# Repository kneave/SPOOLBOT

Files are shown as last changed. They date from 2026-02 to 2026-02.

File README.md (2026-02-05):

# SPOOLBOT
Prusa 2KG Spool Robot

Source Code, Wiring Diagram & BOM for SpoolBot.
Arduino Code is Running on a DF-Robot Romeo Mini ESP32.

Check out the origonal build video here:
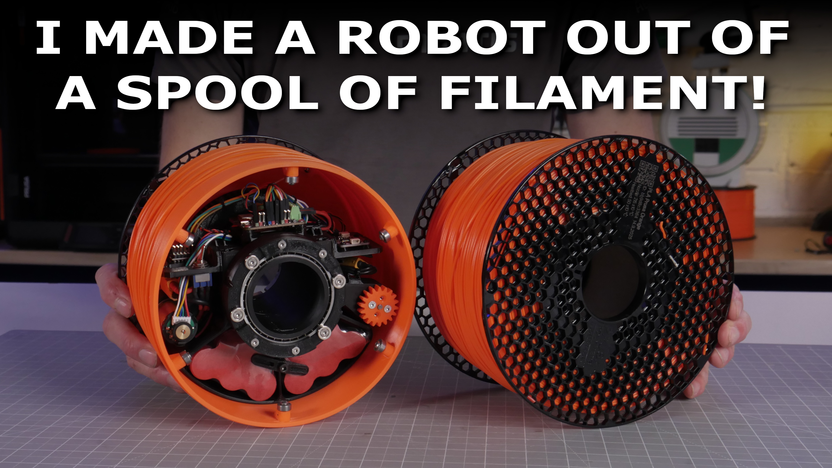
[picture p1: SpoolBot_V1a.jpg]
Watch the video (https://youtu.be/6ZLJA1YpoMs)


STL & CAD Files available at Printables.com
https://www.printables.com/@mantisrobot_2496648
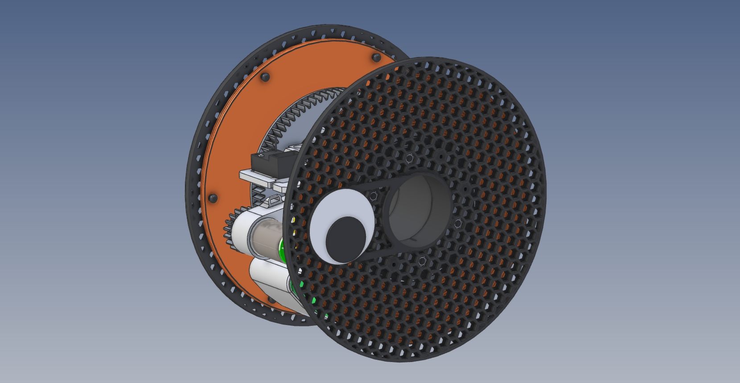
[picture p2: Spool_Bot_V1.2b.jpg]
SpoolBot


SpoolBot Scematic
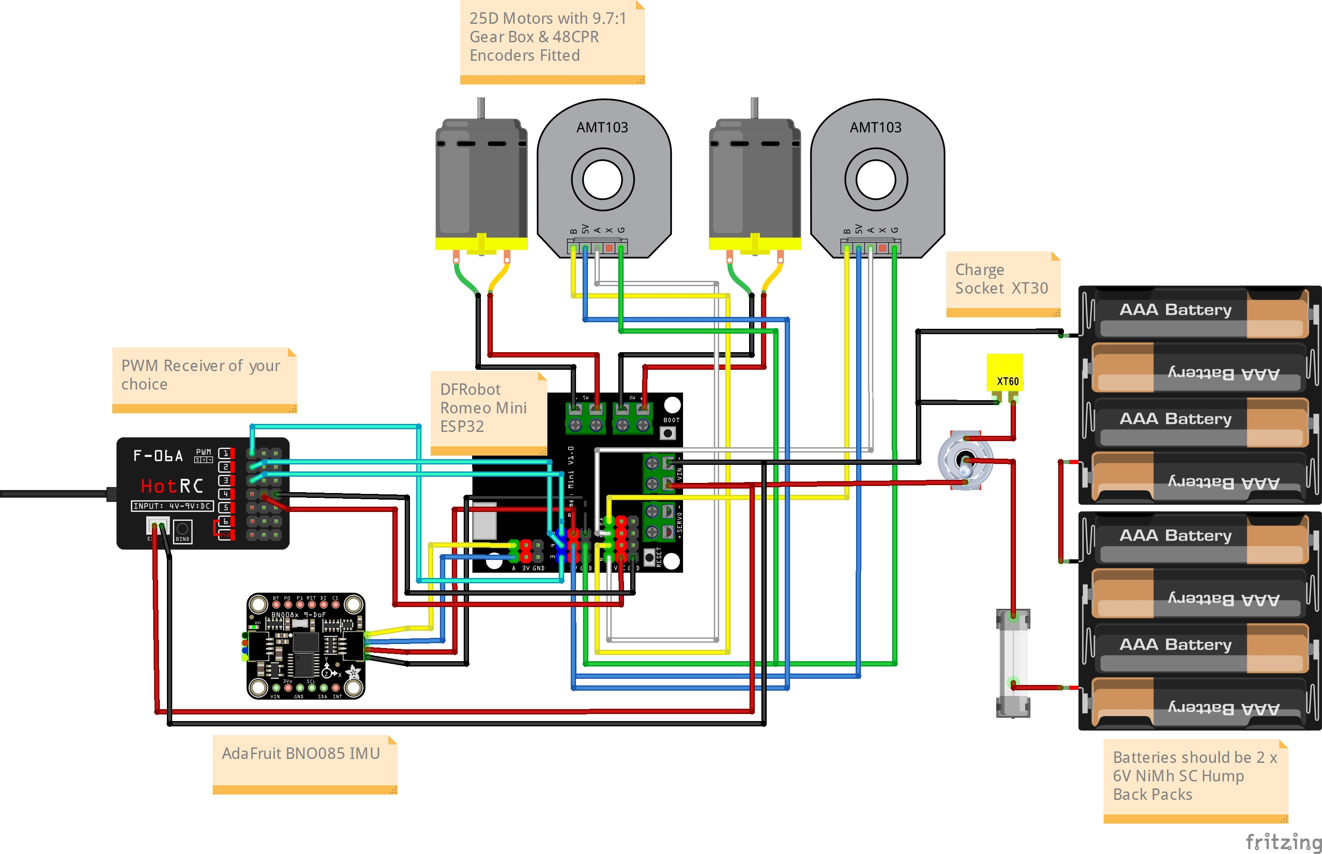
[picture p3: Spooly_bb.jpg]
schematic Schematic


## Parts List
Reference links provided in the [Parts List](./Prusa%20Spool%20Bot%20BOM.xlsx)

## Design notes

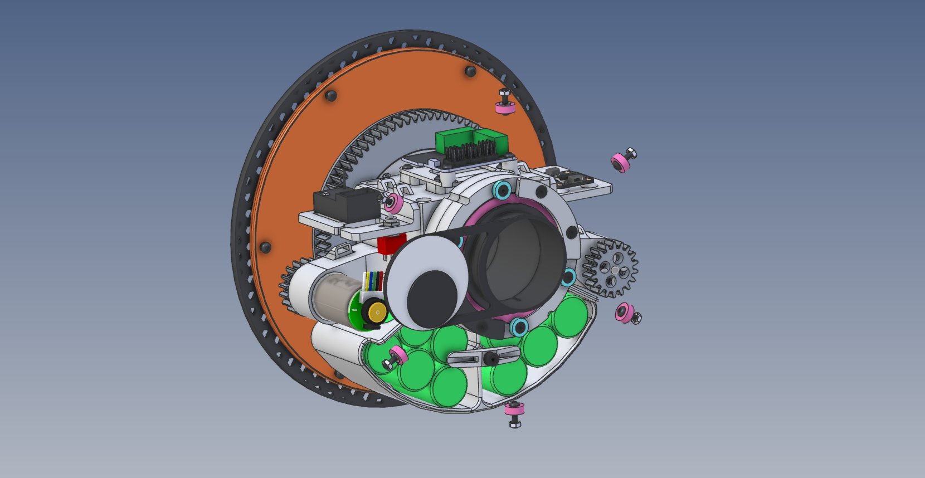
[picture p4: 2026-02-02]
Spool_Bot_V1.2.jpg

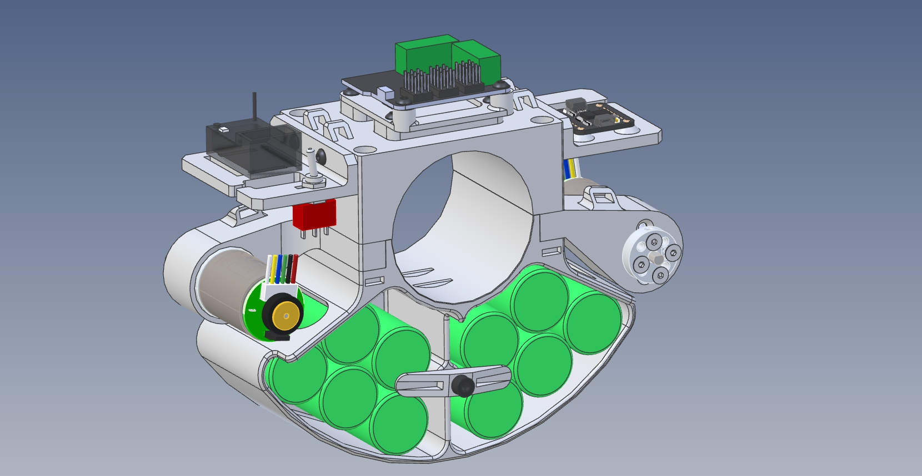
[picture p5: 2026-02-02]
Central_Hub.jpg

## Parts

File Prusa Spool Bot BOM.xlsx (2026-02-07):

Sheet: BOM
Prusa Spool Bot BOM
Part | Description | Qty | Cost | Sub | UK Links | U.S. Links | Notes
1 | 55x68x7mm Bearing 61711 | 4 | £6.73 | £26.92 | 61711 Bearing (https://simplybearings.co.uk/shop/p188629/61711-Budget-Open-Type-Thin-Section-Deep-Groove-Ball-Bearing-55x68x7mm/product_info.html) | https://amzn.to/4qeRzQE | (Shop around local for cheaper)
2 | 10x3x4 Bearing | 6 | £2.23 | £13.38 | 10x3x4 Bearing (https://simplybearings.co.uk/shop/p170604/623ZZ-Budget-Metal-Shielded-Deep-Groove-Ball-Bearing-3x10x4mm/product_info.html) | https://amzn.to/4ajuCWC | (Unknown quality!)
3 | Motor/Encoder | 2 | £61.95 | £123.90 | https://www.pololu.com/product/4862 | https://www.pololu.com/product/4862
4 | Hub Adapter | 1 | £10.95 | £10.95 | https://www.pololu.com/product/1997 | https://www.pololu.com/product/1997
 | M3 Button Head Set | 1 | £5.99 | £5.99 | https://amzn.to/4q6ULh3 | https://amzn.to/4a8HcYu
5 | M3x6 Button Head Socket | 13
6 | M3x12 Button Head | 10
7 | M3x7x0.5 washer | 6
 | M3 Counter Sunk Set | 1 | £5.58 | £5.58 | https://amzn.to/4ragjKA | https://amzn.to/4qXbHI8
8 | M3x6 CS Screw | 12
9 | M3x20 CS Socket | 12
10 | M3 Hex Nut | 6
 | M4 Cap Head Set | 1 | £5.00 | £5.00 | https://amzn.to/4qMgcFp | https://amzn.to/3O3PfhM
11 | M4x25 Cap Head | 9
12 | M4x5 Black cap head | 8 | £3.79 | £3.79 | https://amzn.to/45wr8ye | https://amzn.to/4roa8Tb
13 | M4x8 CS + Nut Black | 4 | £6.58 | £6.58 | https://amzn.to/45ueRdQ | https://amzn.to/4qVIehy
14 | M4 Square Nut | 4
15 | M4 Hex Nut | 8
16 | No.2 x 6.4mm Screw | 4 | £1.39 | £1.39 | https://amzn.to/4bmNia4 | https://amzn.to/4taD7Md
17 | 12x3x4 Magnets | 4 | £9.98 | £9.98 | https://amzn.to/4sokrs0 | https://amzn.to/4c5deai
18 | 10x3x3 Magnets | 4 | £9.99 | £9.99 | https://amzn.to/4qDw7Wc | https://amzn.to/4qhv7q1
19 | 50mm Goolgy Eyes | 1 | £4.19 | £4.19 | https://amzn.to/3YJqABu | https://amzn.to/4aso4G6
20 | M3 Heat Insert | 29
21 | M4 Heat Insert | 5
22 | DF Robot Romeo ESP32 | 1 | £17.00 | £17.00 | DF Robot Romeo ESP32 (https://uk.farnell.com/dfrobot/dfr1063/romeo-mini-control-board-esp32/dp/445737)
23 | 6A Toggle Switch (ON-ON) | 1 | £6.99 | £6.99 | https://amzn.to/3YJVCch | https://amzn.to/4r3gBDC
24 | 18 AWG silicone wire | 1 | £5.99 | £5.99 | https://amzn.to/4qwDm1Z | https://amzn.to/4acHDRK
25 | XT60 Male Connector | 2 | £5.49 | £5.49 | https://amzn.to/4bJrepZ | https://amzn.to/4kcfxKM
26 | Jumper F-F 100mm | 10 | £6.99 | £6.99 | https://amzn.to/49Qc7sr | https://amzn.to/3OiPnKm
27 | Qwiic Connector Jumper | 1 | £1.00 | £1.00 | Qwiic Jumper (https://thepihut.com/products/stemma-qt-qwiic-jst-sh-4-pin-cable-with-premium-female-sockets-150mm-long) | https://www.adafruit.com/product/4397
28 | 6V NiMh Battery Hump Back | 2 | £14.35 | £28.70 | 6V NiMh Battery (https://www.componentshop.co.uk/6v-3300mah-sc-nimh-hump-rc-battery-pack-vapex.html) |  | (Local R/C Shop? 3000 TO 5000MaH)
29 | Adafruit BNO085 | 1 |  | £27.00 | https://amzn.to/4rjBVnJ | https://www.adafruit.com/product/4754
30 | Dupont 0.1” Connector Kit | 1 |  | £7.89 | https://amzn.to/4rjBVnJ | https://amzn.to/49XTeVK
31 | Top RC Transmitter | 1 | £29.89 | £29.89 | https://www.amazon.co.uk/Transmitter-Receiver-Remote-Controller-Channel/dp/B0CH17GR5Y?th=1 | https://www.amazon.com/DS-600-Transmitter-Receiver-Controller-Channel/dp/B09Y8XT53X
32 | Prusament PLA/PETG | 1 | 23.99 | 23.99 |  | https://amzn.to/4a9z8Xh
33 | Prusament PETG | 1 | 23.99 | 23.99 |  | https://amzn.to/3NTPufy
 |  |  |  | £412.56

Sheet: 3D Printed Parts
Item | Name | Qty | Material | Notes
1 | DHG M1.5 18T | 2 | PLA
2 | Fake Side Filament Removable End | 1 | PLA
3 | Fake Side Filament V1.1 | 1 | PLA
4 | Filament Hub V1.1 | 1 | PLA
5 | Removable Side Shim | 1 | PLA
6 | Axle Body Spacer | 2 | PETG
7 | Spool Bearing Holder MAG P2 | 1 | PETG | Magnetic Side (Left)
8 | Spool Bearing Holder MAG P3 | 1 | PETG | Magnetic Side (Left)
9 | Spool Bearing Holder P1 | 2 | PETG | Magnetic Side (Left)
10 | Spool Bearing Holder P1 Fixed | 1 | PETG | Fixed Side (Right)
11 | Spool Bearing Holder P2 | 1 | PETG | Fixed Side (Right)
12 | Spool Bearing Holder P3 | 1 | PETG | Fixed Side (Right)
13 | Axle Lock V1 | 2 | PETG
14 | Battery Mount | 1 | PETG
15 | Battery Stay | 1 | PETG
16 | Central Hub Clamp V1.1 | 1 | PETG
17 | Central Hub | 2 | PETG
18 | IMU Shelf | 1 | PETG
19 | Motor Mount | 2 | PETG
20 | Romeo Mini Mount V1.1 | 1 | PETG
21 | RX Shelf | 1 | PETG
22 | Spool Gear Hub Fixed Side UNITE | 1 | PETG | (Right side)
23 | Spool Gear Hub UNITE 80T | 1 | PETG | (Left Side)
24 | Googly Eye Adapter | 2 | PETG
 | Total Parts | 31

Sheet: Loom
LOOM
Main black and red wire between connectors 300mm long
Short red wire from XT60 to switch middle pin 110mm
Red power wire to terminal block 250mm cut to length
Black charge wire from negative 200mm cut to length
Black power wire from negative 200mm cut to length
Red charge wire from switch 150mm cut to length

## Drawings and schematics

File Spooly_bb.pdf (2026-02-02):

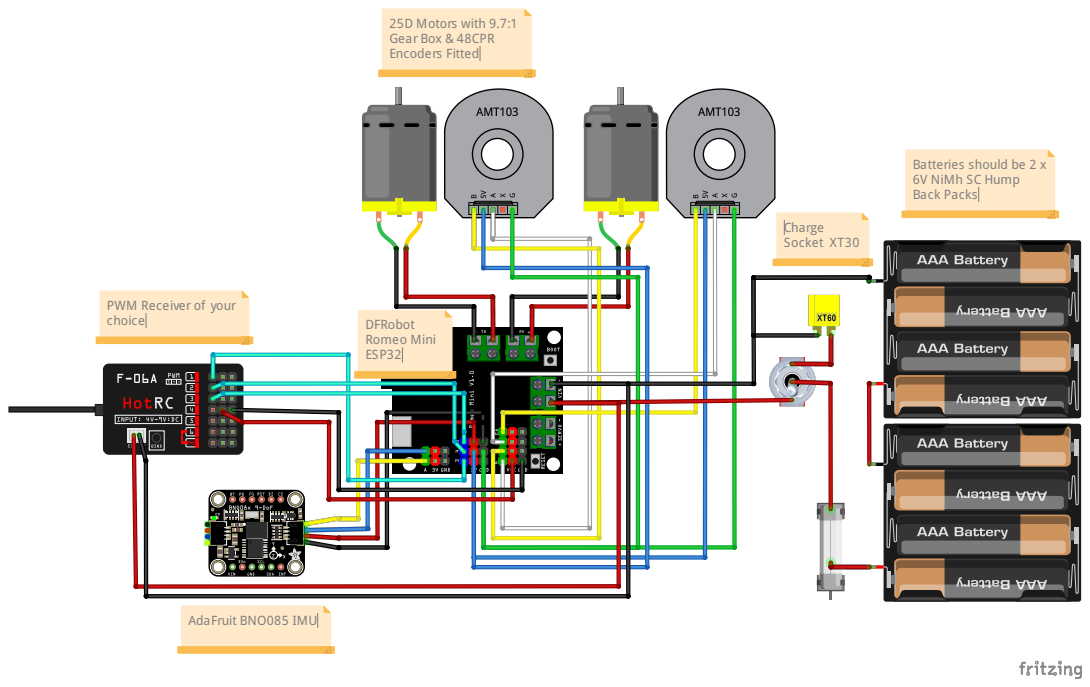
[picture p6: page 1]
Charge Socket XT30; 25D Motors with 9.7:1 Gear Box & 48CPR Encoders Fitted; AdaFruit BNO085 IMU; DFRobot Romeo Mini ESP32

Batteries should be 2 x
6V NiMh SC Hump
Back Packs

PWM Receiver of your
choice

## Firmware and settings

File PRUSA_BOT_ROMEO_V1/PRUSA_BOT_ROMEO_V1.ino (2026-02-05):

// *****************************************************
//  Prusa Spool Bot (Spooly) by Matt Denton 05/02/2026
//  Written for DFRobot Romeo Mini ESP32.
//  Used "ESP32C3 Dev Module" as the device selection.
//  Enable "USB CDC On Boot" for USB debug messages.
//  Requires Adafruit BNO085 IMU.
//
//  Removeable / Magenetc side is the left, Fixed side is right
//  
//  PWM Inputs will require calibration, use the USBC connector to access the serial terminal
//  type 'C' and press enter in the console and follow instructions.
//
//  Some know issues with BNO085 and ESP32 i2c. if you are having problems try adding a 2K2 to 4k7 
//  resistor on the BNO085 from VCC to SDA line
//
// *****************************************************

#include <Arduino.h>
#include <Adafruit_BNO08x.h>
#include <PID.h>
#include <WiFi.h>
#include <WiFiUdp.h>
#include <ArduinoOTA.h>  // For enabling over the air updates
#include "DFRobot_GDL.h"
#include <EEPROM.h>

//  Loop Frequency
#define LOOP_TIME 10 //ms

// *****************************************************
// FEATURE DEFINITIONS

//#define ENABLE_OTA        // Over The Air Updates, switch off once tuning/development is done
//#define ENABLE_UDP_DEBUG  // send / receive UDP debug data for tuning, switch off once tuning is done.
IPAddress pcIP(10,1,0,123);   // your PC IP address for SerialPlot

#define USE_LEDC          // ledcWrite routines rather than analogWrite for Motor PWM
#define PWM_FREQUENCY_SWITCHING // without this only MOTOR_PWM_LO_FREQUENCY is used
#define PWM_HI_FREQ_DUTY         (0.1f) // NORMALISED SO 0.1 = 10%
#define PWM_LO_FREQ_DUTY         (0.05f) // NORMALISED SO 0.05 = 5%
#define MOTOR_PWM_HI_FREQUENCY   8000 // Above PWM_HI_FREQ_DUTY dutr this frequency is used
#define MOTOR_PWM_LO_FREQUENCY   2000 // Belwo PWM_LO_FREQ_DUTY duty this frequency is used

// *****************************************************
// MOTOR SPEED / CONTROL VARIABLES

#define ENC_CPR (48.0f)
#define MOTOR_GEAR_RATIO  (9.7f) // motor attached gearbox
#define PRINTED_GEAR_RATIO  (80.0f/18.0f)

#define MOTOR_MAX_RPM       (8000) // before gearbox, this determines max forward speed
#define RPM_DEADBAND        (100) // RPM
#define MIN_RPM             (0) // provides kick if needed
#define MAX_TURN_SPEED      (540.0f) // degreees /sec

#define TURN_FORWARD_SPEED_REDUCTION 0.35f // reduction in forward speed when turning, this is a sliding scale from 100% to this value.
#define PITCH_CURVE 0.35f                 // IMU Pitch sigmoid curve, lower values = higher brakeing, 1 = linear 
#define HALF_SPEED_REDUCTION      (0.6f)  // user control speed reduction for forward / reverse
#define HALF_SPEED_TURN_REDUCTION (0.6f)  // user control speed reduction for turn

// *****************************************************
// IMU / CONTROL VARIABLES USED FOR NORMALISING IMU DATA

#define IMU_PITCH_MAX (75.0f) // at this angle the motor is in full reverse to prevent looping
#define IMU_ROLL_MAX (50.0f)  // fall/tilt angle motors off 
#define IMU_YAW_MAX (50.0f)
#define IMU_PITCH_RATE_MAX (360.0f)
#define IMU_ROLL_RATE_MAX (360.0f)
#define IMU_YAW_RATE_MAX (MAX_TURN_SPEED) // determins max turn speed

// *****************************************************
//  PINS

#define MOTA_ENCA  6
#define MOTA_ENCB  7
#define MOTB_ENCA  20
#define MOTB_ENCB  21

#define PWM_PITCH  4
#define PWM_YAW    3
#define PWM_AUX    5

#define MOTA_DIR   1
#define MOTA_PWM   0
#define MOTB_DIR   10
#define MOTB_PWM   2

// *****************************************************
//  PID VARIABLES & INSTANCES

// left motor / magnetic removable side
float  lDesiredRpm=0, lMeasuredRpm=0, lDriveOutput=0;
std::PID lPid(&lMeasuredRpm, &lDriveOutput, &lDesiredRpm,3.2f,6.8f,0.12f, DIRECT); // 0.00012, 0.0005
// right motor / fixed side
float  rDesiredRpm=0, rMeasuredRpm=0, rDriveOutput=0;
std::PID rPid(&rMeasuredRpm, &rDriveOutput, &rDesiredRpm,3.2f,6.8f,0.12f, DIRECT); // 0.2, 3.5, 0.001
// turn PID
float  measuredYaw=0, setYaw=0, yawOutput=0;
std::PID yawPid(&measuredYaw, &yawOutput, &setYaw,0.35f,2.0f,0.005f, DIRECT); // 0.2, 3.5, 0.001

// variables sued in control caluculations and in experimental speed PID
float pitchOutput=0,measuredSpeed=0;


// *****************************************************
// trim variables used during remote tuning of PID loops
float trimTemp = PITCH_CURVE;
float pTrim = 0.001;
float iTrim = 0.012f;
float dTrim = 0.0f;

#define PTRIM_INC 0.0001f  // 0.05
#define ITRIM_INC 0.001f  // 0.05
#define DTRIM_INC 0.00001f // 0.001

// *****************************************************
//  IMU

Adafruit_BNO08x  bno08x(-1);
sh2_SensorValue_t sensorValue;


// *****************************************************
// global variables

unsigned long previousMillis = 0;
bool  initialBoot = true; // must be cleared by user input before motors can be enabled on initial boot.
bool  motorsEnabled = false;  // user motor kill switch
bool  headingHoldAlways = false;  // hold heading even when no user input
bool  positionHoldAlways = true;  // hold position rather than drift if nudged
bool  userControl = false; // is there a desired move from user controls
bool  halfSpeed = false;  // finer speed control
bool  halfSpeedTurn = true;  // finer speed control

float  normPitch=0,normRoll=0,normPitchRate=0,normYawRate=0,pitchCurve=0;
float  measuredSpeedFiltered=0;

// encoder outputs
float EncA_SpeedFiltered = 0; // filtered encoder speeds
float EncB_SpeedFiltered = 0;
float WheelA_OutputSpeed = 0; // calculated wheel speeds
float WheelB_OutputSpeed = 0;

// loop delta variables
uint32_t  loopLastUs = 0;
uint32_t  loopDeltaUs = 0;
float loopDelta = 0;

// user controls
uint16_t  pitch_PWM = 1500;
uint16_t  yaw_PWM = 1500;
uint16_t  aux_PWM = 1500;
float pitch_controlFiltered = 0;  // filtered user controls
float yaw_controlFiltered = 0;
float aux_controlFiltered = 0;
float pitch_controlFinal = 0;     // final user controls after all filters applied
float yaw_controlFinal = 0;

// Gyro Structure
typedef struct {
  float x;
  float y;
  float z;
} gyro_s;

// gyro filtered data
gyro_s gyroF;

// *****************************************************
// Calibration data

struct __attribute__((packed)) PWMCal {
  uint16_t min_raw;   // 
  uint16_t max_raw;   // 
  uint16_t mid_raw;   // 
};

struct __attribute__((packed)) CalStore {
  uint32_t magic;     // 0x50454431 
  PWMCal pitch;
  PWMCal yaw;
  uint16_t crc;       // simple sum or 0xFFFF if unused
};

#define PWM_MAX (2000)  // uS
#define PWM_MID (1500)
#define PWM_MIN (1000)  // uS
#define CAL_MAGIC 0x50454431
CalStore calData;

// *****************************************************
void setup() {
  
  pinMode(MOTA_ENCA, INPUT_PULLUP);
  pinMode(MOTA_ENCB, INPUT_PULLUP);
  pinMode(MOTB_ENCA, INPUT_PULLUP);
  pinMode(MOTB_ENCB, INPUT_PULLUP);
  pinMode(PWM_PITCH, INPUT_PULLDOWN);
  pinMode(PWM_YAW, INPUT_PULLDOWN);
  pinMode(PWM_AUX, INPUT_PULLDOWN);
  setupMotorPins();
  
  //  Start Serial and wait for connection 2 seconds
  Serial.begin(115200);
  int t = 20;
  while (!Serial && t--) delay(100);
  Serial.println("\r\nPrusa Spool Bot (Spooly) by Matt Denton\r\n");

  // configure WiFi
  #if defined(ENABLE_OTA) || defined(ENABLE_UDP_DEBUG)
  setupWiFi();
  #endif

  // Try to initialize IMU
  while (!bno08x.begin_I2C()) 
  {
    Serial.println("Failed to find BNO08x chip");
    delay(200);
  }
  Serial.println("BNO08x Found!");

  // report IMU data
  for (int n = 0; n < bno08x.prodIds.numEntries; n++) 
  {
    Serial.print("Part ");
    Serial.print(bno08x.prodIds.entry[n].swPartNumber);
    Serial.print(": Version :");
    Serial.print(bno08x.prodIds.entry[n].swVersionMajor);
    Serial.print(".");
    Serial.print(bno08x.prodIds.entry[n].swVersionMinor);
    Serial.print(".");
    Serial.print(bno08x.prodIds.entry[n].swVersionPatch);
    Serial.print(" Build ");
    Serial.println(bno08x.prodIds.entry[n].swBuildNumber);
  }

  // set IMU events
  BNOSetEvents();

  // configure Motor Encoders
  initEncoders();

  // configure interupt pins
  attachInterrupt(digitalPinToInterrupt(MOTA_ENCA), EncA_isrAB, CHANGE);
  attachInterrupt(digitalPinToInterrupt(MOTA_ENCB), EncA_isrAB, CHANGE);
  attachInterrupt(digitalPinToInterrupt(MOTB_ENCA), EncB_isrAB, CHANGE);
  attachInterrupt(digitalPinToInterrupt(MOTB_ENCB), EncB_isrAB, CHANGE);
  attachInterrupt(digitalPinToInterrupt(PWM_PITCH), pwm_pitch_isr, CHANGE);
  attachInterrupt(digitalPinToInterrupt(PWM_YAW), pwm_yaw_isr, CHANGE);
  attachInterrupt(digitalPinToInterrupt(PWM_AUX), pwm_aux_isr, CHANGE);

  // load PWM calibration data
  loadCal();
  Serial.println("Cal after load:");
  Serial.printf("  magic=%x\r\n",calData.magic);
  Serial.printf("  pitch[min,mid,max]=[%d,%d,%d]\r\n",calData.pitch.min_raw,calData.pitch.mid_raw,calData.pitch.max_raw);
  Serial.printf("  yaw[min,mid,max]=[%d,%d,%d]\r\n",calData.yaw.min_raw,calData.yaw.mid_raw,calData.yaw.max_raw);
  CalStore chk=calData; 
  uint16_t expect; 
  chk.crc=0; 
  expect=simple_crc(chk);
  Serial.printf("  crc stored=%x expect=%x\r\n",calData.crc,expect);

  // configure left motor PID
  lPid.SetOutputLimits(-1, 1);
  lPid.SetSampleTime(LOOP_TIME);
  lPid.SetMode(AUTOMATIC);

  // configure right motor PID
  rPid.SetOutputLimits(-1, 1);
  rPid.SetSampleTime(LOOP_TIME);
  rPid.SetMode(AUTOMATIC);

  // configure turn rate/yaw PID
  yawPid.SetOutputLimits(-1, 1);
  yawPid.SetSampleTime(LOOP_TIME);
  yawPid.SetMode(AUTOMATIC);

  // initialise encoder variables
  noInterrupts();
  resetEncoders();
  initRPMCDF();
  initSpeedCDF();
  interrupts();

  // start
  loopLastUs = micros();
  Serial.println("Loop..");
}

// *****************************************************
void loop() 
{

  #if defined(ENABLE_OTA) || defined(ENABLE_UDP_DEBUG)
  wifiService();
  #endif

  BNOService();  
  checkUserCommands();

  if (millis() - previousMillis >= LOOP_TIME) 
  {    
    previousMillis = millis();
    
    // read volatile encoder values
    updateEncoders();
    // read new PWM user control values
    updatePWMControls();
    // update loop delta variables
    updateLoopVariables();
    // fitler encoders using FOF
    //FOF_EncoderFilter();
    // filter encoders using critical damped filter
    RPMCdf();
    // filter PWM user controls
    filterPWM();
    // Check user control inputs & Configuration mode
    checkControlInputs();
    // Filter & Normailse IMU date to +/-1
    normailseIMUData();
    // Compute the forward and turn speed using control inputs and IMU data
    computeDriveVariables();
    // update motors
    updateDriveMotors(pitchOutput ,yawOutput );
    // turn off motors on tip over
    rollOverProtection();

    #ifdef ENABLE_UDP_DEBUG
    udpPacketReceive();
    sendWiFiUDPDataStream();
    #endif

    // Serial Debug Messages
    //debugEncoder();
    //debugAHRS();
    //debugPWM();
    //debugOutput();
  
  }

}


void computeDriveVariables()
{ 

  // Setup initial drive speed, All normalised values +/-1.0
  float bodyPitchSpeed = pitch_controlFinal;
  // reduce speed if required
  if( halfSpeed ) bodyPitchSpeed *= HALF_SPEED_REDUCTION;
  // reduce body speed when turning to prevent roll over, this is a graded
  // reduction from 100% down to TURN_FORWARD_SPEED_REDUCTION %
  bodyPitchSpeed *= 1.0-( fabs(yaw_controlFiltered) * TURN_FORWARD_SPEED_REDUCTION );

  // calucalte measured speed of wheels using motor RPM and offset gyro rotations
  // to remove body climbing the wheel gear. Sort of works
  measuredSpeed = ((-WheelA_OutputSpeed + WheelB_OutputSpeed)/2.0f) + (gyroF.y/6.0f);
  measuredSpeedFiltered = speedCdf();

  // calculate curved pitch, this gives much better braking control rather than a linear pitch output
  // effectively makes IMY less responsive when alligneds with ground, Spooly stationary.
  pitchCurve = sigmoidCurve(normPitch,PITCH_CURVE);

  // Calculate the pitchOutput depending on what mode we are in
  // if we dont want to adjust position when nudged or on a hill
  if( positionHoldAlways == true ) 
  {
    // higher rate gain when holding position and no pitch gain
    if( userControl == false ) pitchOutput = normPitchRate * 0.5f;
    else pitchOutput = bodyPitchSpeed + pitchCurve + normPitchRate * 0.05f;
  }
  // otherwise always allow drift
  else
  {
    pitchOutput = bodyPitchSpeed + pitchCurve + normPitchRate * 0.05f;
  }

  // Update YAW PID variables
  measuredYaw = normYawRate;
  setYaw = yaw_controlFinal;//yaw_controlFiltered;
  // reduce for half speed turn
  if( halfSpeedTurn ) setYaw *= HALF_SPEED_TURN_REDUCTION;
  // if heading hold is off and there is no user input, do not adjust yaw control
  // we dont want the integrator to wind up so we disable PID updates when not in use.
  if( headingHoldAlways == false ) 
  {
    if( (userControl == false || motorsEnabled == false ) && yawPid.GetMode() == AUTOMATIC )
    {
      Serial.println("YAW PID = Off");
      yawPid.SetMode(MANUAL);
      yawOutput = 0;
    }      
    else if( userControl == true && yawPid.GetMode() == MANUAL )
    {
      Serial.println("YAW PID = On");
      yawPid.SetMode(motorsEnabled);
    }
  }
  else
  {
    yawPid.SetMode(motorsEnabled);
  }

  
  // Compute YAW PID
  yawPid.Compute();

}


void  updateDriveMotors( float pForwardSpeed, float pYawSpeed )
{
  float leftMotorRpm,rightMotorRpm;

  // tank drive mix
  leftMotorRpm = (pForwardSpeed + pYawSpeed);// * MOTOR_MAX_RPM;
  rightMotorRpm = (pForwardSpeed - pYawSpeed);// * MOTOR_MAX_RPM;
   
  //clamp drive to MAX
  leftMotorRpm = constrain(leftMotorRpm,-1.0f,1.0f);
  rightMotorRpm = constrain(rightMotorRpm,-1.0f,1.0f);

  // normalise encoder speed
  lMeasuredRpm = EncA_SpeedFiltered/MOTOR_MAX_RPM;
  rMeasuredRpm = EncB_SpeedFiltered/MOTOR_MAX_RPM;

  // if motors are off, set speed to 0 and disable PID to prevent windup
  if( motorsEnabled == false )
  {
    leftMotorRpm = 0;
    rightMotorRpm = 0;
    lDriveOutput = 0;
    rDriveOutput = 0;
    lPid.SetMode(MANUAL);
    rPid.SetMode(MANUAL);
  }
  else
  {
    lPid.SetMode(AUTOMATIC);
    rPid.SetMode(AUTOMATIC);
  }

  // LEFT MOTOR
  // invert left side drive here
  lDesiredRpm = -leftMotorRpm;

  // deadband and minimum punch rpm
  if( fabs(lDesiredRpm) <= (RPM_DEADBAND/MOTOR_MAX_RPM) ) lDesiredRpm = 0;
  #if MIN_RPM > 0
  else if( lDesiredRpm > (RPM_DEADBAND/MOTOR_MAX_RPM) && lDesiredRpm < (MIN_RPM/MOTOR_MAX_RPM) ) lDesiredRpm = (MIN_RPM/MOTOR_MAX_RPM);
  else if( lDesiredRpm < (-RPM_DEADBAND/MOTOR_MAX_RPM) && lDesiredRpm > (-MIN_RPM/MOTOR_MAX_RPM) ) lDesiredRpm = (-MIN_RPM/MOTOR_MAX_RPM);
  #endif


  if( lPid.Compute() )
  {
    // apply max duty
    lDriveOutput = constrain(lDriveOutput,-1.0f,1.0f);
  }


  // RIGHT MOTOR
  // invert right side drive here
  rDesiredRpm = rightMotorRpm;

    // deadband and minimum punch rpm
  if( fabs(rDesiredRpm) <= (RPM_DEADBAND/MOTOR_MAX_RPM) ) rDesiredRpm = 0;
  #if MIN_RPM > 0
  else if( rDesiredRpm > (RPM_DEADBAND/MOTOR_MAX_RPM)  && rDesiredRpm < (MIN_RPM/MOTOR_MAX_RPM) ) rDesiredRpm = (MIN_RPM/MOTOR_MAX_RPM);
  else if( rDesiredRpm < (-RPM_DEADBAND/MOTOR_MAX_RPM)  && rDesiredRpm > (-MIN_RPM/MOTOR_MAX_RPM) ) rDesiredRpm = (-MIN_RPM/MOTOR_MAX_RPM);
  #endif


  if( rPid.Compute() )
  {
    // apply max duty
    rDriveOutput = constrain(rDriveOutput,-1.0f,1.0f);
  }

  updateMotorAPWM(lDriveOutput);
  updateMotorBPWM(rDriveOutput);
  

}




void rollOverProtection()
{
  // roll over protection
  if( fabs(normRoll) >= 0.99f && motorsEnabled == true )
  {
    motorsEnabled = false;
    initialBoot = true;
    userControl = false;
    Serial.println("Roll Over Motors Off!");
  }
}


void checkControlInputs()
{
  // check aux input for enable / disable
  // must be disabled first if initialBoot flag is true
  if( aux_controlFiltered < -0.5 )
  {
    initialBoot = false;
    if( motorsEnabled == true ) 
    {
      motorsEnabled = false;
      Serial.println("Motors Disabled!");
      userControl = false;
      Serial.println("Moveing Stop.");
    }
  }
  else if( aux_controlFiltered > 0.5 )
  {      
    if( motorsEnabled == false && initialBoot == false )
    {
      motorsEnabled = true;
      Serial.println("Motors Enabled!");
    }
  }

  // set moving / stopped flag using user controls and current motor speeds
  // this is used for switching modes / braking etc
  if( motorsEnabled == true )
  {
    if( fabs(pitch_controlFiltered) > 0.005f || fabs(yaw_controlFiltered) > 0.005f )
    {
      if( userControl == false )
      {
        userControl = true;
        Serial.println("Moveing..");
      }
    }
    else if( fabs(lMeasuredRpm) < (50.0f/MOTOR_MAX_RPM) && fabs(rMeasuredRpm) < (50.0f/MOTOR_MAX_RPM) )
    {
      if( userControl == true )
      {
        userControl = false;
        Serial.println("Moveing Stop.");
      }
    }
  }

  // config mode enabled when motors off
  #define PROGRAM_MODE_THRESHOLD (0.95f)
  if( motorsEnabled == false && initialBoot == false  )
  {
    pitch_controlFinal = 0;
    yaw_controlFinal = 0;

    // Toggle position hold mnode / brake when no user input
    int t = 25;
    // user must hold positon fo 1 second to set mode
    while( pitch_controlFiltered > PROGRAM_MODE_THRESHOLD && t-- ) {keepAlive();}
    if( pitch_controlFiltered > PROGRAM_MODE_THRESHOLD )
    {
      positionHoldAlways = !positionHoldAlways;
      Serial.print("Forward Position Hold = ");
      Serial.println(positionHoldAlways);
      while(fabs(pitch_controlFiltered) > 0.5f ) keepAlive();      
      Serial.println("OK");
    }

    // Toggle half forward speed
    t = 25;
    while( pitch_controlFiltered < -PROGRAM_MODE_THRESHOLD && t-- ) {keepAlive();}
    if( pitch_controlFiltered < -PROGRAM_MODE_THRESHOLD )
    {
      halfSpeed = !halfSpeed;
      Serial.print("Half Speed = ");
      Serial.println(halfSpeed);
      while(fabs(pitch_controlFiltered) > 0.5f ) keepAlive();     
      Serial.println("OK");
    }      

    // Toggle Heading Hold mode
    t = 25;
    while( yaw_controlFiltered > PROGRAM_MODE_THRESHOLD && t-- ) {keepAlive();}
    if( yaw_controlFiltered > PROGRAM_MODE_THRESHOLD )
    {
      headingHoldAlways = !headingHoldAlways;
      Serial.print("Heading Hold = ");
      Serial.println(headingHoldAlways);
      while(fabs(yaw_controlFiltered) > 0.5f ) keepAlive();     
      Serial.println("OK");
    }

    // Toggle half turn speed
    t = 25;
    while( yaw_controlFiltered < -PROGRAM_MODE_THRESHOLD && t-- ) {keepAlive();}      
    if( yaw_controlFiltered < -PROGRAM_MODE_THRESHOLD )
    {
      halfSpeedTurn = !halfSpeedTurn;
      Serial.print("Half Speed Turn = ");
      Serial.println(halfSpeedTurn);
      while(fabs(yaw_controlFiltered) > 0.5f ) keepAlive();    
      Serial.println("OK");
    }      

  }

}

// polls critical routines while in config mode
void keepAlive()
{
  BNOService();
  #if defined(ENABLE_OTA) || defined(ENABLE_UDP_DEBUG)
  wifiService();
  #endif
  updateEncoders();
  updatePWMControls();
  updateLoopVariables();
  filterPWM();
  #ifdef ENABLE_UDP_DEBUG
  sendWiFiUDPDataStream();
  #endif  
  delay(20);
}


// user inputs via serial used for trimming and calibration
void checkUserCommands()
{  
  while( Serial.available() )
  {
    char c = Serial.read();
    switch(c)
    {
      case 'P':
        pTrim += PTRIM_INC;
        Serial.print("P = ");
        Serial.println(pTrim);
        break;
      case 'p':
        pTrim -= PTRIM_INC;
        if( pTrim < 0 ) pTrim = 0;
        Serial.print("P = ");
        Serial.println(pTrim);
        break;
      case 'I':
        iTrim += ITRIM_INC;
        Serial.print("I = ");
        Serial.println(iTrim);
        break;
      case 'i':
        iTrim -= ITRIM_INC;
        if( iTrim < 0 ) iTrim = 0;
        Serial.print("I = ");
        Serial.println(iTrim);
        break;
      case 'D':
        dTrim += DTRIM_INC;
        Serial.print("D = ");
        Serial.println(dTrim);
        break;
      case 'd':
        dTrim -= DTRIM_INC;
        if( dTrim < 0 ) dTrim = 0;
        Serial.print("D = ");
        Serial.println(dTrim);
        break;              
      case '>':
        trimTemp += 0.01;
        Serial.print("Trim = ");
        Serial.println(trimTemp);
        break;
      case '<':
        trimTemp -= 0.01;
        Serial.print("Trim = ");
        Serial.println(trimTemp);
        break;
      case 'C':
        runCalibration();
        break;
    }
  }
}


void updateLoopVariables()
{
  // calculate loop delta variables
  uint32_t usNow = micros();
  loopDeltaUs = usNow - loopLastUs;   // OK across wrap-around for unsigned
  loopLastUs = usNow;
  if (loopDeltaUs < 500 ) return; // ignore silly-small dt
  loopDelta = loopDeltaUs * 1e-6f;
}

/*
 * interpolation routine
 */


float interpolate( float x, float inlo, float inhi, float outlo, float outhi )
{
  
  if( x > inhi ) return outhi;
  else if( x < inlo ) return outlo;
  
  return (   outlo + ( ( ( x - inlo ) * (outhi - outlo) ) / (inhi-inlo) ) );
}



void debugOutput()
{
    Serial.print("A MEAS:");
    Serial.print(lMeasuredRpm);
    Serial.print(", DES:");
    Serial.print(lDesiredRpm);  
    Serial.print(", OUT:");
    Serial.println(lDriveOutput);  
    //Serial.print(", HZ:");
    //Serial.print(ledcReadFreq(MOTA_PWM));
    //Serial.print(", PWM");
    //Serial.println(ledcRead(MOTA_PWM));    

    Serial.print(" B MEAS:");
    Serial.print(rMeasuredRpm);
    Serial.print(", DES:");
    Serial.print(rDesiredRpm);  
    Serial.print(", OUT:");
    Serial.println(rDriveOutput);  
    //Serial.print(", HZ:");
    //Serial.print(ledcReadFreq(MOTB_PWM));
    //Serial.print(", PWM:");
    //Serial.println(ledcRead(MOTB_PWM));    
}

void debugPWM()
{
    Serial.print("PWM P:");
    Serial.print(pitch_controlFiltered,3);
    Serial.print(",Y:");
    Serial.print(yaw_controlFiltered,3);  
    Serial.print(",A:");
    Serial.println(aux_controlFiltered,3);  
}
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

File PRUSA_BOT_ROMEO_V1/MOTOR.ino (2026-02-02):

#define MOTOR_PWM_RANGE        ((1 << MOTOR_PWM_RESOLUTION) - 1)

// *****************************************************
// MOTOR CONTROL MODE
#ifdef  USE_LEDC
#define MOTOR_PWM_RESOLUTION  10
#else
#define MOTOR_PWM_RESOLUTION  8
#endif

bool  motA_HiFreq = false;
bool  motB_HiFreq = false;


void setupMotorPins()
{
  pinMode(MOTA_DIR, OUTPUT);
  pinMode(MOTB_DIR, OUTPUT);
  digitalWrite(MOTA_DIR,0);
  digitalWrite(MOTB_DIR,0);
  #ifdef USE_LEDC
  ledcAttach(MOTA_PWM, MOTOR_PWM_LO_FREQUENCY, MOTOR_PWM_RESOLUTION);
  ledcAttach(MOTB_PWM, MOTOR_PWM_LO_FREQUENCY, MOTOR_PWM_RESOLUTION);
  ledcWrite(MOTA_PWM,0);
  ledcWrite(MOTB_PWM,0);
  #else
  analogWriteFrequency(MOTA_PWM,MOTOR_PWM_LO_FREQUENCY);
  analogWriteFrequency(MOTB_PWM,MOTOR_PWM_LO_FREQUENCY);
  analogWriteResolution(MOTA_PWM,MOTOR_PWM_RESOLUTION);
  analogWriteResolution(MOTB_PWM,MOTOR_PWM_RESOLUTION);
  analogWrite(MOTA_PWM,0);
  analogWrite(MOTB_PWM,0);
  #endif
}

void updateMotorAPWM(float duty)
{

  float aduty = fabs(duty);
  float a = interpolate(aduty,0.0f,1.0f,0,MOTOR_PWM_RANGE);

  if( motorsEnabled == false ) a = 0;

  #ifdef PWM_FREQUENCY_SWITCHING
  configurePWMFrequency(MOTA_PWM,aduty,&motA_HiFreq);
  #endif

  if(duty < 0 ) 
  {
    if( !digitalRead(MOTA_DIR) ) 
    {
      #ifdef USE_LEDC
      ledcWrite(MOTA_PWM,0);
      #else
      analogWrite(MOTA_PWM,0);
      #endif
      digitalWrite(MOTA_DIR,1);
    }
    #ifdef USE_LEDC
    ledcWrite(MOTA_PWM,a);
    #else
    analogWrite(MOTA_PWM,a);
    #endif
  }
else 
  {
    if( digitalRead(MOTA_DIR) ) 
    {
      #ifdef USE_LEDC
      ledcWrite(MOTA_PWM,0);
      #else
      analogWrite(MOTA_PWM,0);
      #endif
      digitalWrite(MOTA_DIR,0);
    }
    #ifdef USE_LEDC
    ledcWrite(MOTA_PWM,a);
    #else
    analogWrite(MOTA_PWM,a);
    #endif
  }
}

void updateMotorBPWM(float duty)
{
  float aduty = fabs(duty);
  float a = interpolate(aduty,0.0f,1.0f,0,MOTOR_PWM_RANGE);

  if( motorsEnabled == false ) a = 0;

  #ifdef PWM_FREQUENCY_SWITCHING
  configurePWMFrequency(MOTB_PWM,aduty,&motB_HiFreq);
  #endif

  if(duty < 0 ) 
  {
    if( !digitalRead(MOTB_DIR) ) 
    {
      #ifdef USE_LEDC
      ledcWrite(MOTB_PWM,0);
      #else
      analogWrite(MOTB_PWM,0);
      #endif
      digitalWrite(MOTB_DIR,1);
    }
    #ifdef USE_LEDC
    ledcWrite(MOTB_PWM,a);
    #else
    analogWrite(MOTB_PWM,a);
    #endif
  }
else 
  {
    if( digitalRead(MOTB_DIR) ) 
    {
      #ifdef USE_LEDC
      ledcWrite(MOTB_PWM,0);
      #else
      analogWrite(MOTB_PWM,0);
      #endif
      digitalWrite(MOTB_DIR,0);
    }
    #ifdef USE_LEDC
    ledcWrite(MOTB_PWM,a);
    #else
    analogWrite(MOTB_PWM,a);
    #endif
  }
}


void configurePWMFrequency(int motPin, float aduty, bool *mode)
{
if( aduty > PWM_HI_FREQ_DUTY && *mode == false ) 
  {
    #ifdef USE_LEDC
    ledcChangeFrequency(motPin,MOTOR_PWM_HI_FREQUENCY,MOTOR_PWM_RESOLUTION);
    #else
    analogWriteFrequency(motPin,MOTOR_PWM_HI_FREQUENCY);
    #endif
    *mode = true;
  }
else if ( aduty < PWM_LO_FREQ_DUTY && *mode == true )
  {
    #ifdef USE_LEDC
    ledcChangeFrequency(motPin,MOTOR_PWM_LO_FREQUENCY,MOTOR_PWM_RESOLUTION);
    #else
    analogWriteFrequency(motPin,MOTOR_PWM_LO_FREQUENCY);
    #endif
    *mode = false;
  }
}

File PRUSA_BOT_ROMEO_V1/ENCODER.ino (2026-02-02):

volatile int32_t EncA_encCount = 0;
volatile uint8_t EncA_prevState = 0;
volatile int32_t EncA_encLastCount = 0;
int32_t          EncA_newCount = 0;
int32_t          EncA_deltaCounts = 0;

volatile int32_t EncB_encCount = 0;
volatile uint8_t EncB_prevState = 0;
volatile int32_t EncB_encLastCount = 0;
int32_t          EncB_newCount = 0;
int32_t          EncB_deltaCounts = 0;

float EncA_Speed = 0;
float EncB_Speed = 0;
float MotA_OutputSpeed = 0;
float MotB_OutputSpeed = 0;

void  initEncoders()
{
  EncA_prevState = readAB(MOTA_ENCA,MOTA_ENCB);
  EncB_prevState = readAB(MOTB_ENCA,MOTB_ENCB);
}

void resetEncoders()
{
  EncA_encLastCount = EncA_encCount;
  EncB_encLastCount = EncB_encCount;
}

void  updateEncoders()
{
  noInterrupts();
  EncA_newCount = EncA_encCount;
  EncB_newCount = EncB_encCount;
  interrupts();

  EncA_deltaCounts = EncA_newCount - EncA_encLastCount;
  EncB_deltaCounts = EncB_newCount - EncB_encLastCount;
  EncA_encLastCount = EncA_newCount;
  EncB_encLastCount = EncB_newCount;

}

inline uint8_t readAB(int A, int B) {
  // pack A as bit1, B as bit0
  uint8_t a = digitalRead(A) ? 1 : 0;
  uint8_t b = digitalRead(B) ? 1 : 0;
  return (a << 1) | b;
}

// Lookup table for quadrature transitions.
// Index = (prev<<2) | curr. Value = -1,0,+1
const int8_t qdec[16] = {
   0, -1, +1,  0,
  +1,  0,  0, -1,
  -1,  0,  0, +1,
   0, +1, -1,  0
};

void EncA_isrAB() {
  uint8_t curr = readAB(MOTA_ENCA,MOTA_ENCB);
  uint8_t idx = (EncA_prevState << 2) | curr;
  EncA_encCount += qdec[idx];
  EncA_prevState = curr;
}

void EncB_isrAB() {
  uint8_t curr = readAB(MOTB_ENCA,MOTB_ENCB);
  uint8_t idx = (EncB_prevState << 2) | curr;
  EncB_encCount += qdec[idx];
  EncB_prevState = curr;
}

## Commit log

2026-02-02 BOM Update
    [Prusa Spool Bot BOM.xlsx]
2026-02-03 Updated BOM
    Added 3D parts list sheet with images
    [Prusa Spool Bot BOM.xlsx]
2026-02-04 Fritzing Update
    Wiring Diagram Updated, SDA/SCL transposed.
    [Spooly.fzz]
2026-02-07 Added Top RC tx to BOM
    [Prusa Spool Bot BOM.xlsx]
